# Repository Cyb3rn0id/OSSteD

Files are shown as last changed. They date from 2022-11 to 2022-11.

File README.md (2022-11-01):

# OSSteD
OSSteD stands for: Old School Stepper Driver
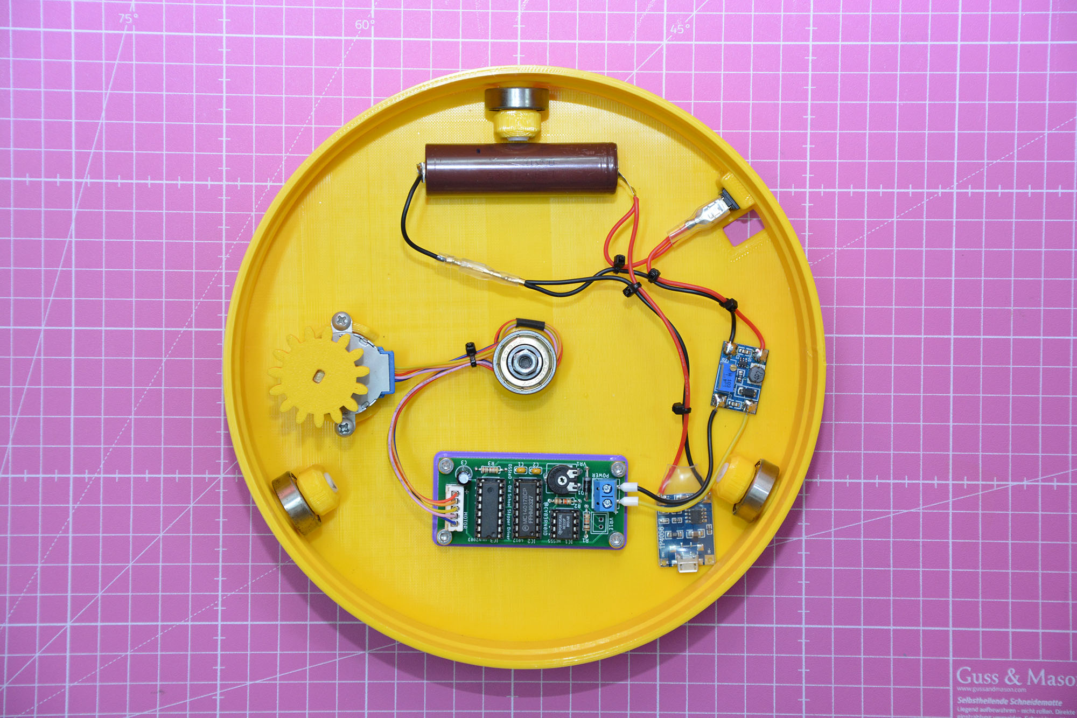
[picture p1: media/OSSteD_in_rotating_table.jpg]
OSSteD mounted

This is an _old style_ stepper driver thought to be used with the popular _28BYJ-48_ Stepper Motor. I created this circuit for using it in conjunction with the [Rotating Table by Basement Creations](https://www.thingiverse.com/thing:4817279) I use for displaying object or taking videos of my stuff.

### Why "Old Style" ?
Times ago a couple of friends 3Dprinted that Rotating Table and built a stepper driver using an Arduino. When they published pictures of their work on social networks, some people complained about that saying things like:  

> This can be achieved using an NE555 too! Why waste a microcontroller?  
 
Yes, but that can be done using also 4 pushbuttons and putting a trained monkey in front of them that pushes buttons one at time sequentially but I did't read comment like this, very strange IMHO. It's clear that every task can be fullfilled in a lot of different ways but there is always someone ready to criticize because looks like we humans are made for this.

Anyway, since I had a lot of ancient ICs in my drawers (One of my hobbies is to repair vintage stuff) and I wanted to refresh some old electronics I learned during my school years, I made the stepper controller using an NE555, a decade counter and a darlington array IC. Now the remaining part of people can say stuff like:

> Why use so old components? They're fuc*ing expensive nowadays! An ATmega328 would be more cheap!  

Making all people happy to criticize every other's project. So, first than criticize, please let me see your trained monkey device. 

### How it works
An NE555 is configured as Astable Oscillator : this means the expensive NE555 will produce a square wave continuously. In this configuration frequency is determined by R1, R2 and C1 in the schematic. I keep fixed C1 at 100nF and R1 at 10K so you can vary frequency by varying R2. For R2 I used a 10K resistor in series to a 100K trimmer. Since frequency of astable oscillator is determined by formula:  
  
`f=1.44/((R1 + 2*R2)*C1)`

when trimmer is set to zero, R2=10K and then frequency is 480Hz (motor at maximum speed), then trimmer is all turned R2=110K and then frequency=62Hz.
I designed the PCB so you can use a trimmer mounted on PCB (VR1) OR an external potentiometer to be mounted on panel and attached to VR1E connector : only one of those 2 must be used.  
  
Frequency output from NE555 is sent to a 4017 decade counter for generating pulse waves for driving the 4 coils of the stepper motor from outputs  0,1,2,3. Output 4 is sent to reset input for making cycle start again. 4017 outputs are connected to an ULN2003 for the power driving. Usually you can obtain a small board with an ULN2003 together that motor when you buy it: from that board you can recover the IC, the IC socket and the motor connector.

### Notes
The 28BYJ-48 Stepper Motor is very slow so if you planned to use this motor like me, you can consider to put your phone in time-lapse mode for having a more fast video or you can elaborate the video after for increasing the speed. This motor has also a very low torque so must be used with a rotating plate having a reduction like the one I've linked in the introduction: many designs on internet connects that motor directly on the plate, this is no good and probably will fail (I've 3D printed one of this plate and as expected motor wasn't able to spin the table).

I found measures of the Rotating Table by Basement Creations has non accurate measures so probably you'll work a lot with file for adjusting parts and fit the  ball-bearings.

### BOM
* IC1	: NE555
* IC2	: CD4017
* IC3	: ULN2003 *
* R1	: 10K&#937; &#188;W
* R2	: 10K&#937; &#188;W
* R3	: 1K&#937; &#188;W
* C1	: 100nF 
* C2	: 100nF
* C3	: 10&#181;F 10V
* VR1	: Trimmer 100K&#937; **
* VR1E	: 2-pin JST-XH pcb male connector (+ external 100K potentiometer) **
* POWER	: 2-pin Screw Terminal
* MOTOR	: 5-pin JST-XH pcb male connector *

(*) You can salvage those components (+1 16 pin DIP IC socket) from a 28BYJ-48 Kit as one linked below
(**) Mount only 1: the VR1 Trimmer OR the VR1E connector+external potentiometer

Optionals:
* 1x 8-pin DIP IC socket
* 2x 16-pin DIP IC socket

### PCB
You can buy the pcb, and then support me, following those 2 steps:

Step 1: Subscribe to PCBWay using my invite link: [https://www.tinyurl.com/pcbwaysz](https://www.tinyurl.com/pcbwaysz)  
Step 2: Order the OSSteD PCB from the following link: [https://tinyurl.com/osstedpcb](https://tinyurl.com/osstedpcb)  

### STL
For an easy mounting internally to the rotating plate I designed a small stand: you can glue that stand internally to the plate and then screw the PCB on top of that stand using 4 M3 6mm screws

### Attachments
- [PCB Stand STL](./stl/OSSteD_stand.stl)
- [Schematic](./docs/OSSteD_schematic.pdf)
- [Gerbers](./gerbers) => Or [buy directly a PCB from PCBWay](https://tinyurl.com/osstedpcb)  
- [Datasheets](./docs/datasheets/)

### Other parts you need
If you want to build the rotating table I linked at top and you're italian you can support me buying those needed parts from Amazon through my affiliate links:

- [4x 608zz Ball-bearings](https://amzn.to/3tIHFfq)
- [1x 28BYJ-48 5V Stepper Motor](https://amzn.to/3Ojb8Vc)*

(*) That kit contains a small board too: from that board you can salvage the ULN2003 IC (IC3), the 16-pin DIP IC socket and the 5-pin JST-XH PCB male connector (MOTOR)

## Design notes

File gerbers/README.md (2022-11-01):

# OSSteD Gerber files
Here are the Gerber files if you want to do PCB by yourself, but you can support me buying the PCB from PCB-way following those 2 steps:

Step 1: Subscribe to PCBWay using my invite link: [https://www.tinyurl.com/pcbwaysz](https://www.tinyurl.com/pcbwaysz)  
Step 2: Order the OSSteD PCB from the following link: [https://tinyurl.com/osstedpcb](https://tinyurl.com/osstedpcb)

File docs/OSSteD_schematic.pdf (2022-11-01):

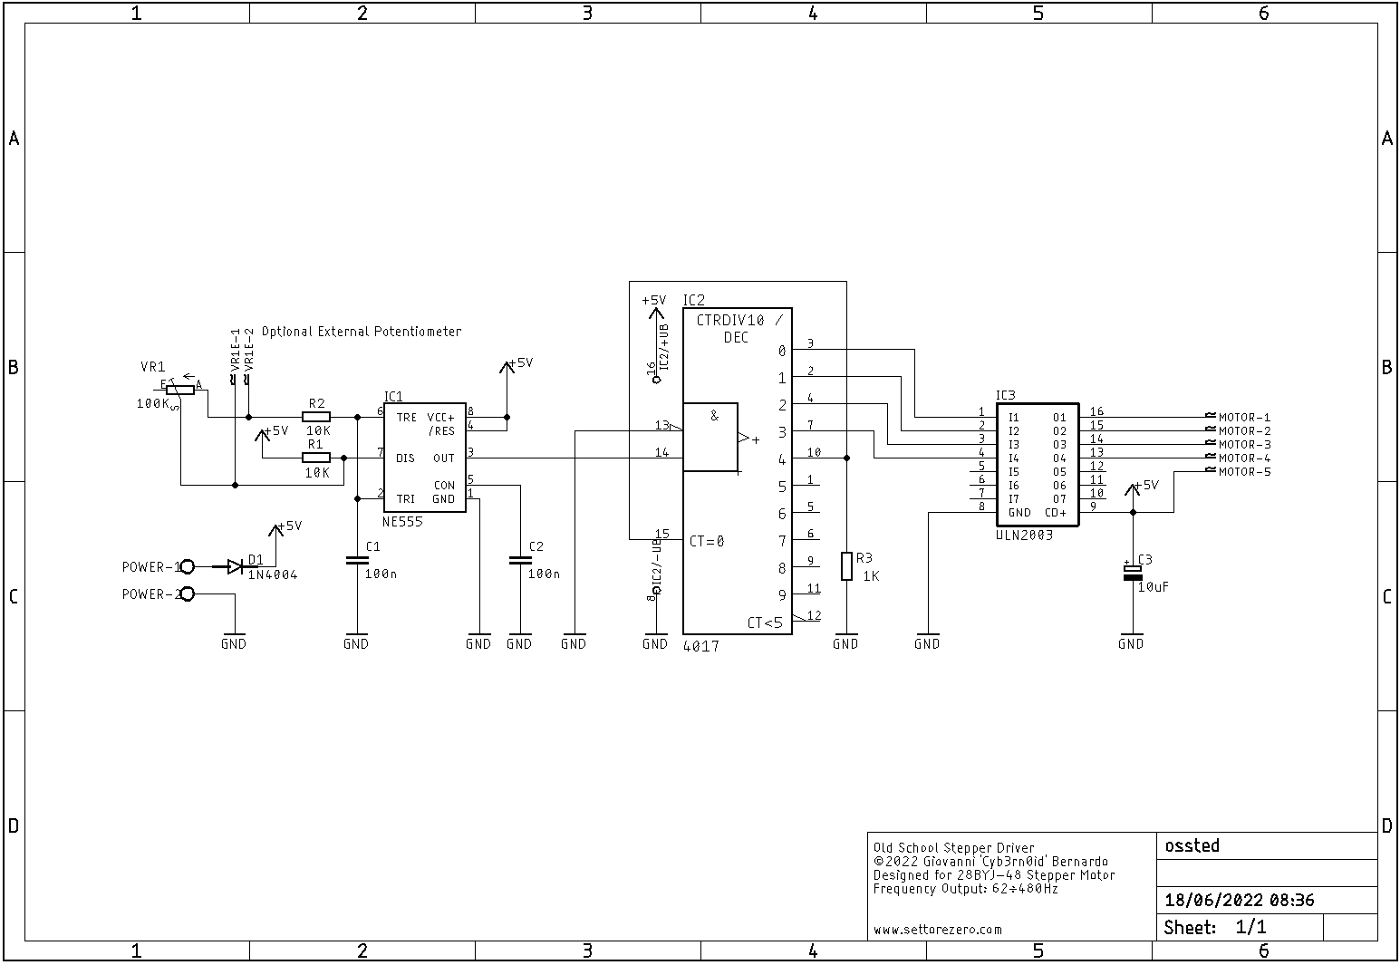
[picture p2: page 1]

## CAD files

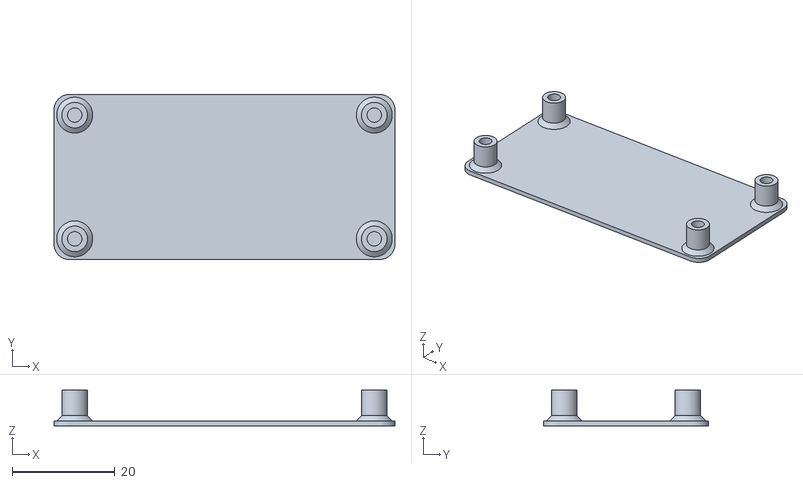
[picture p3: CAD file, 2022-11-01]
stl/OSSteD_stand.stl
66.5 x 32.2 x 7.00
